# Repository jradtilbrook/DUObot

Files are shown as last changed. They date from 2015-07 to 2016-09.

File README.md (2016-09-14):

# DUObot Project Repository

This repository contains the files related to my two-wheeled balancing robot, aptly named DUObot.

In the extremely rare circumstance that someone actually uses this repository and/or finds a bug, please let me know by opening an issue. I would also welcome any other feedback or contributions.

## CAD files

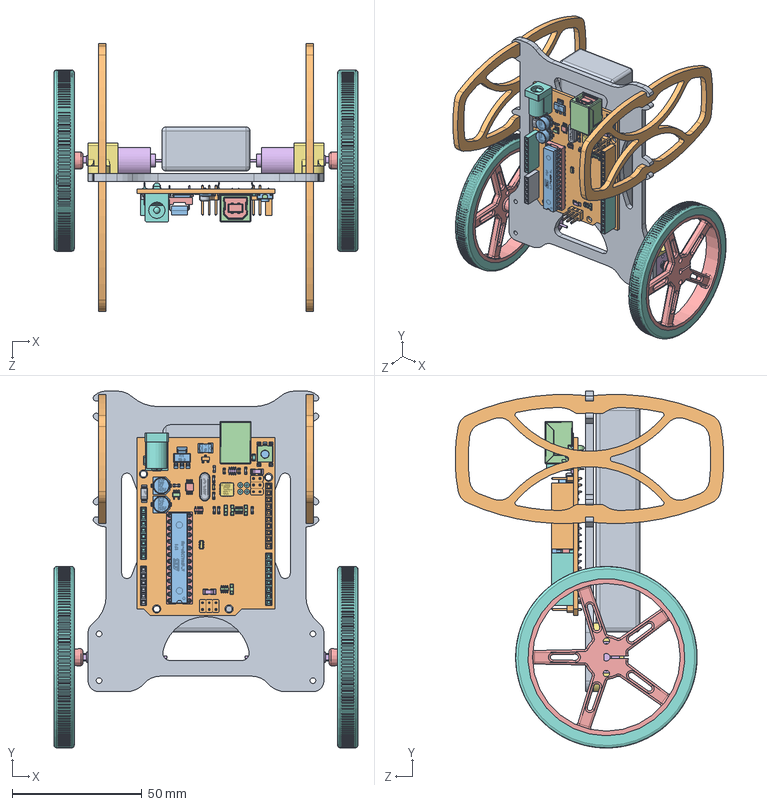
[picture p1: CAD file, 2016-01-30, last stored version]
cad/DUObot.SLDASM
117.2 x 137.7 x 103.6 mm
riser
unoboard blue
47uf CAP Dcase x 2
USB SHELL
USB core
usb top contact x 2
usb btm contact x 2
power jack
crystal
2pin_header__02 x 6
nano - reg
led x 4
dip28
dip socket pin x 28
atmega16u2
8 PORT HEADER x 2
6 PORT HEADER
10 PORT HEADER
ATMEL328P
102 RESISTOR PACK x 2
103 RESISTOR PACK
220 RESISTOR PACK
16mhz crystal - measured
PADS001
603 cap on pad x 8
ssot3
mf-msmf050-2
lmv358
lp2985dgkr
cd1206 diode x 2
603 resistor
blm21
m7 diode
MLC0603 x 2
RESET CORE
RESET
Pololu 70mm Wheel x 2
12mm Motor Gearbox x 2
mount x 2
Pololu 70mm Tire x 2
battery
guard x 2

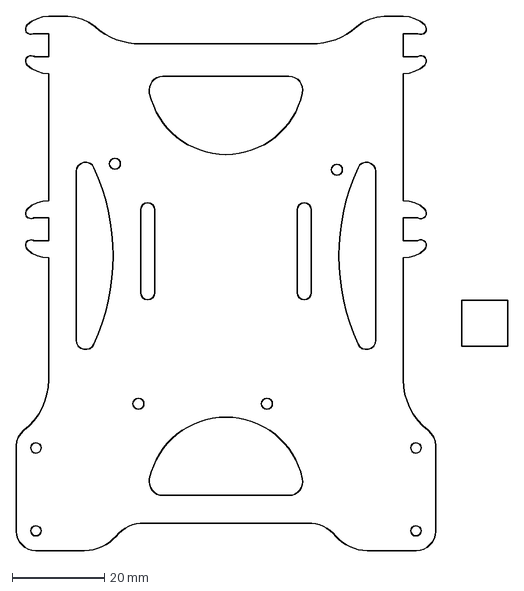
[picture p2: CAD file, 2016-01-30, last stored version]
cad/riser_final.dxf
106.7 x 116.0 mm

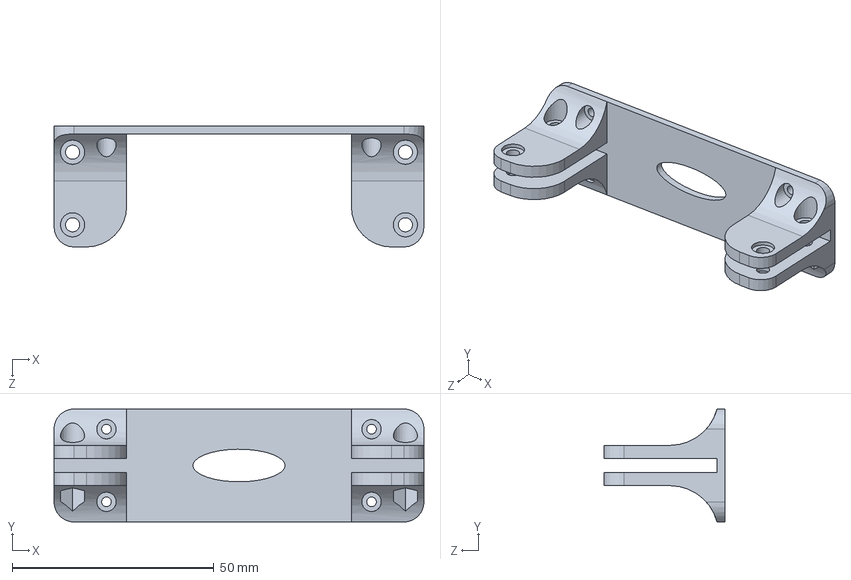
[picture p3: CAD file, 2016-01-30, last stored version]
cad/motor-riser-adapter.SLDPRT
91.7 x 28.0 x 30.0 mm

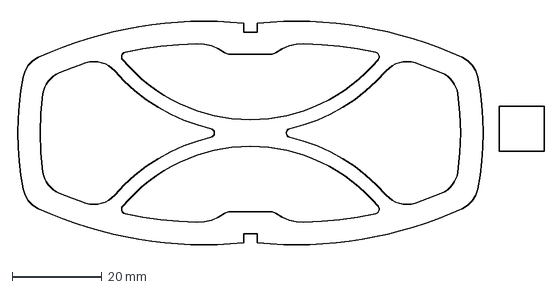
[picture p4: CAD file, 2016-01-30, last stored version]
cad/guard_final.dxf
117.6 x 52.0 mm

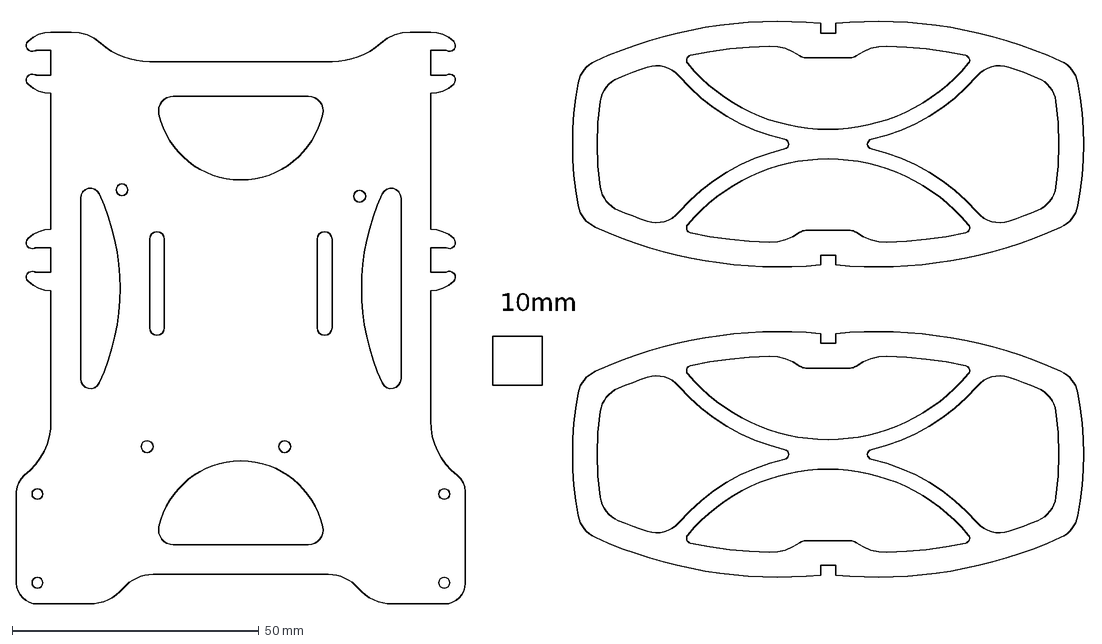
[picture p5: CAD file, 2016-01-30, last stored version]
cad/DUO_mk4.dxf
10mm

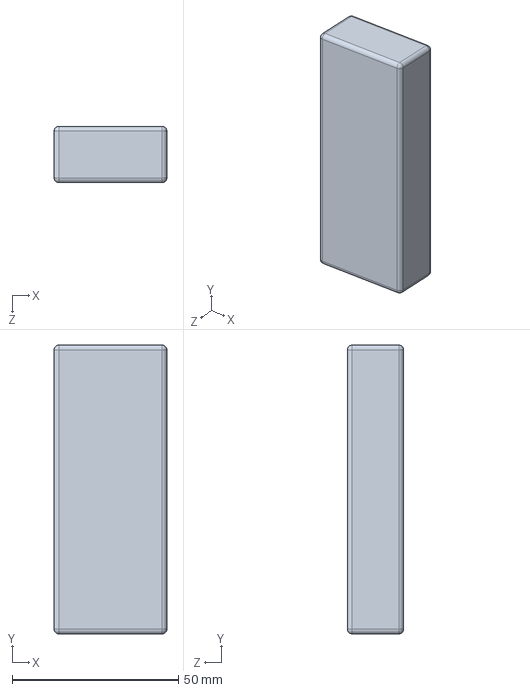
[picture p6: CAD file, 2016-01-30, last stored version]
cad/battery.SLDPRT
34.0 x 87.0 x 17.0 mm

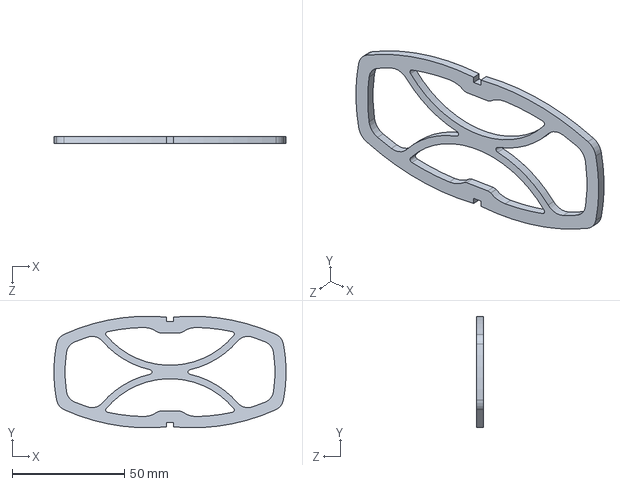
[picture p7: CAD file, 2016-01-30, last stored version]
cad/guard.SLDPRT
103.6 x 49.8 x 3.00 mm

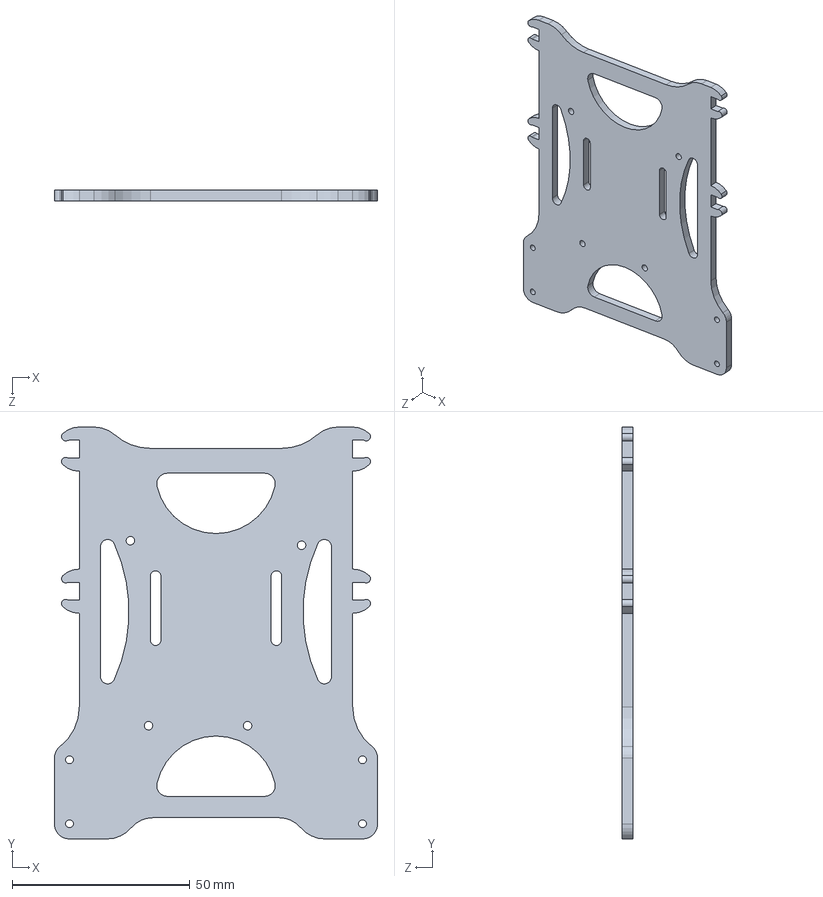
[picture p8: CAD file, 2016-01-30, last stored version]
cad/riser.SLDPRT
91.0 x 116.0 x 3.00 mm

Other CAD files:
cad/DUO_mk4.dwg
cad/guard.DXF
cad/motor-riser-adapter.STL
cad/riser.DXF

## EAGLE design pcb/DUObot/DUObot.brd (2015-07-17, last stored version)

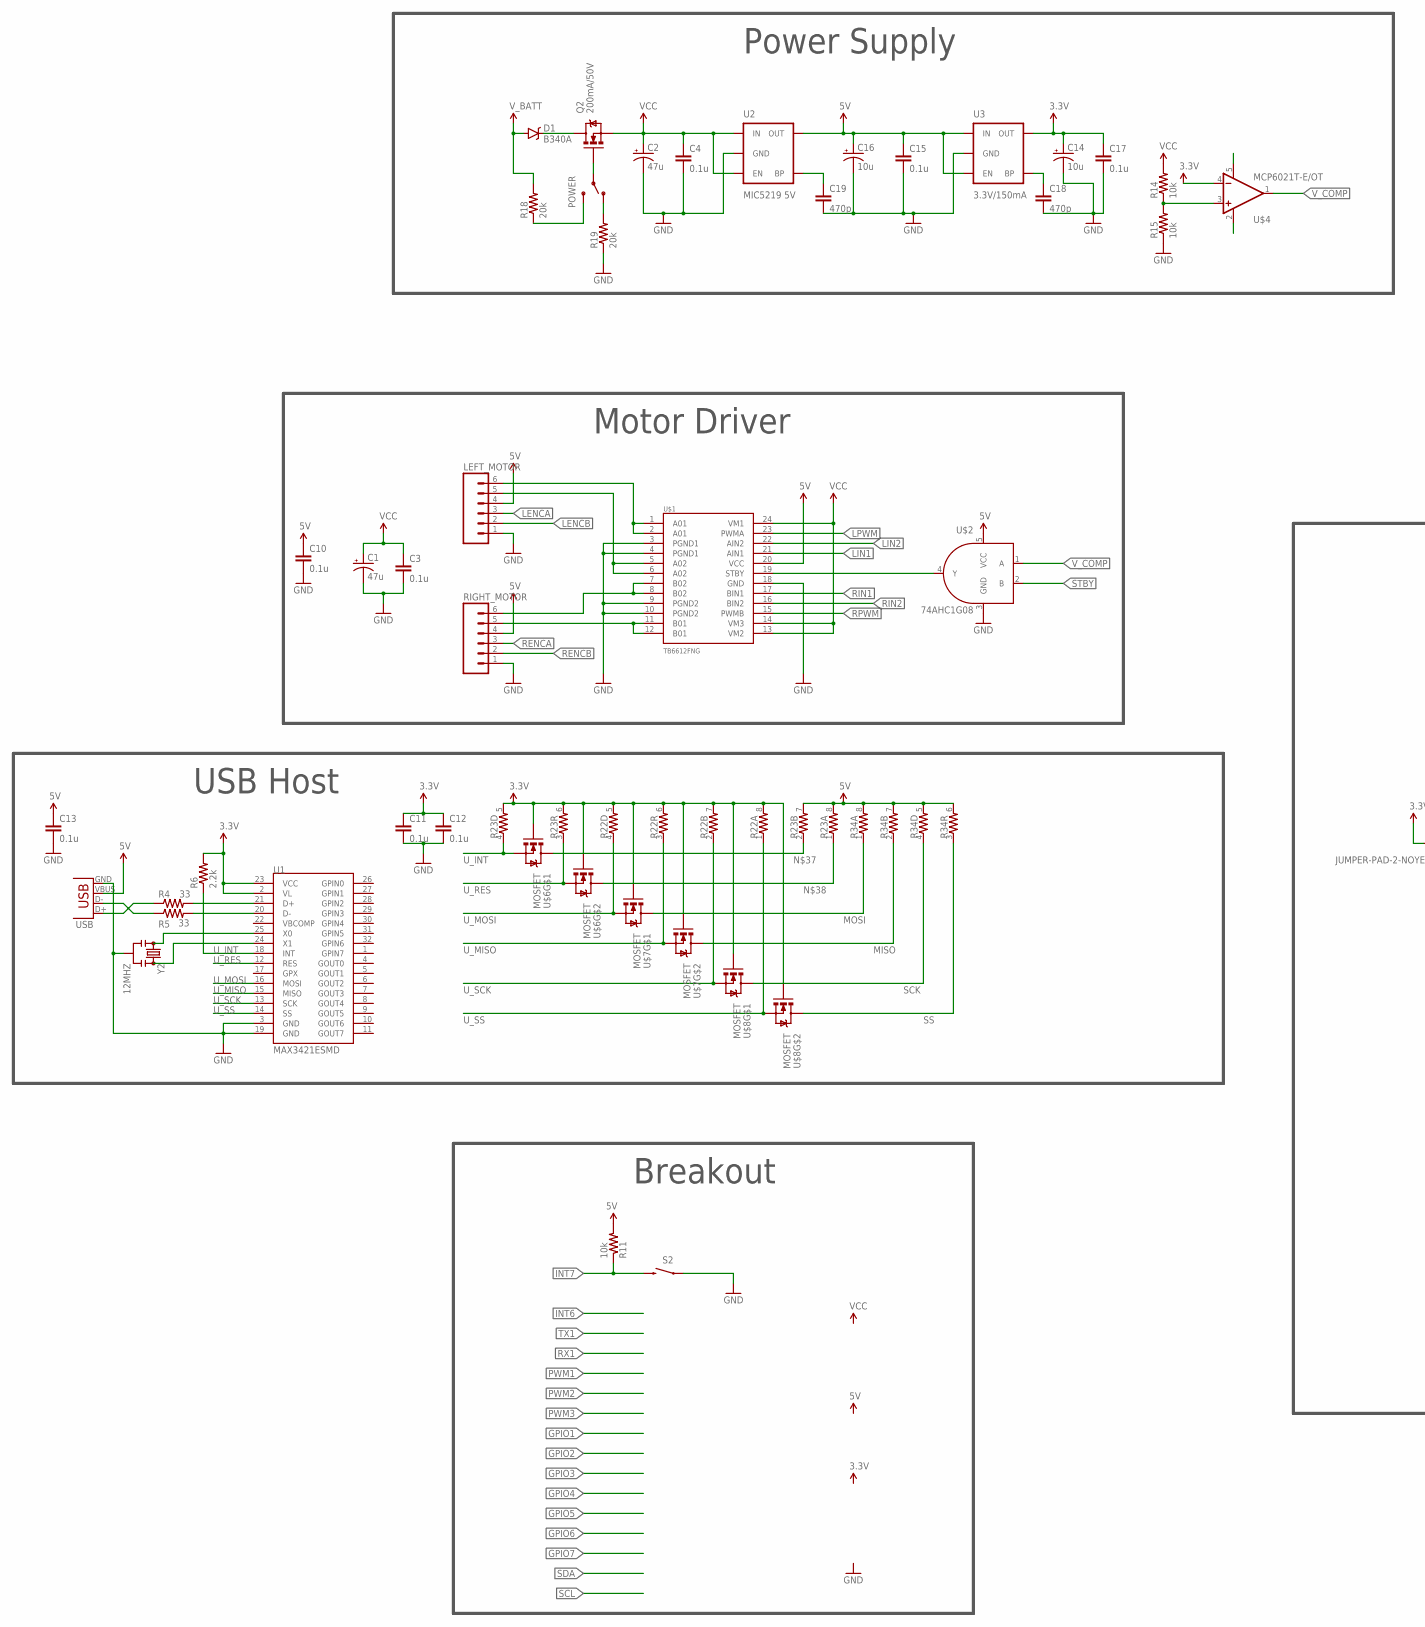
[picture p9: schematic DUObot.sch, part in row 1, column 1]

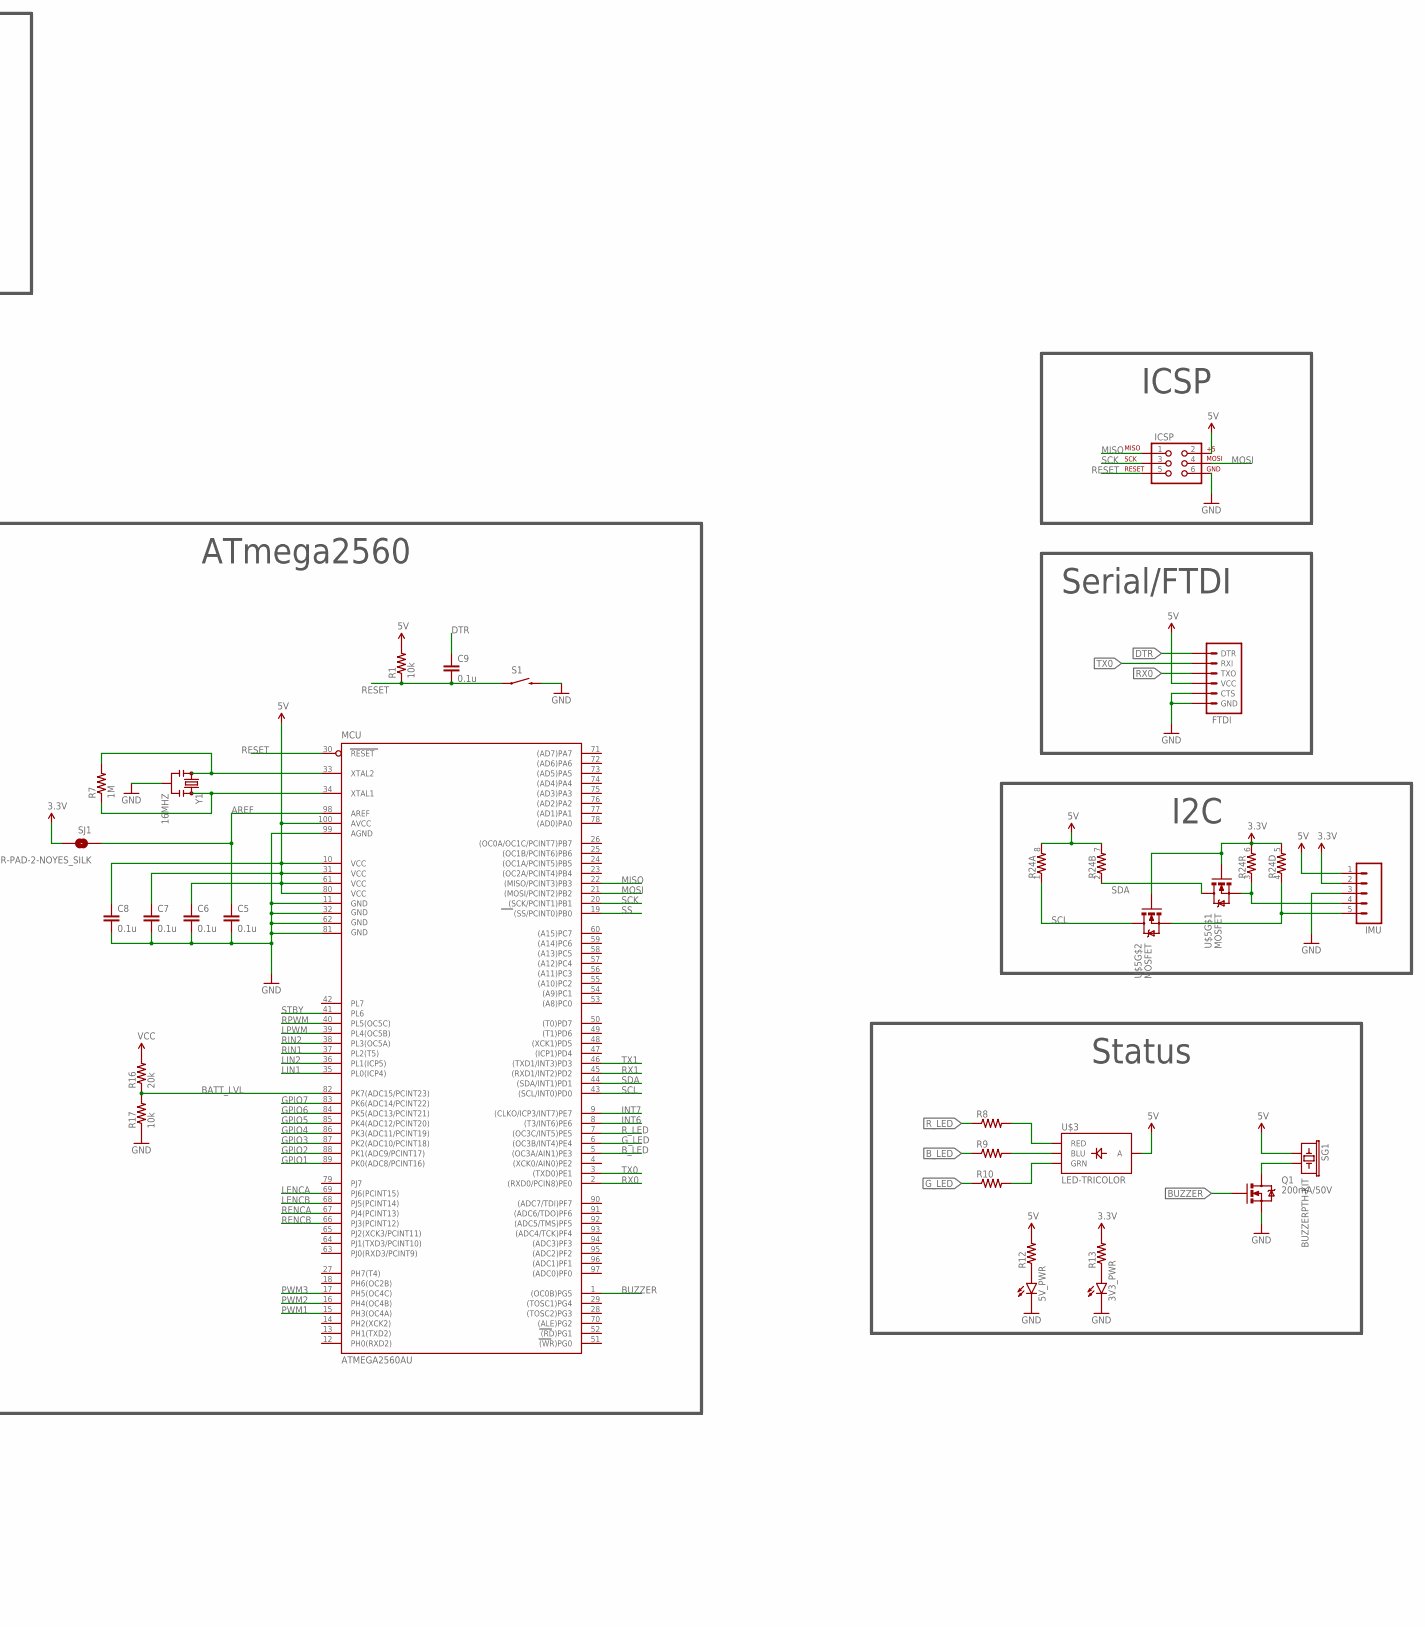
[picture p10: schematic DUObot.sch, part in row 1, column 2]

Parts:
3V3_PWR, 5V_PWR: LED0805; LED-0805
C1, C2: 47u; PANASONIC_D
C3, C4, C5, C6, C7, C8, C9, C10, C11, C12, C13, C15, C17: 0.1u; 0805
C14, C16: 10u; EIA3216
C18, C19: 470p; 0805
D1: B340A; SMA-DIODE
FTDI: ARDUINO_SERIAL_PROGRAMPTH; 1X06
ICSP: AVR_SPI_PRG_6TESTPOINTS; 2X3_TEST_POINTS
IMU: M05SMD2; 1X05-1MM-RA
LEFT_MOTOR: M06SMD-1MM; 1X06-1MM
MCU: ATMEGA2560AU; TQFP100
POWER: SWITCH-SPDT-SMD-A; SWITCH-SPST-SMD-A
Q1, Q2: 200mA/50V; SOT23-3
R1, R11, R14, R15, R17: 10k; 0805
R4, R5: 33; 0805
R6: 2.2k; 0805
R7: 1M; 0805
R8, R9, R10, R12, R13: RESISTOR0805-RES; 0805
R16, R18, R19: 20k; 0805
R22, R23, R24, R34: RESISTOR-ARRAY0603-ARV; 0603-ARV
RIGHT_MOTOR: M06SMD-1MM; 1X06-1MM
S1, S2: SWITCH-MOMENTARY-2SMD-4; TACTILE_SWITCH_TALL
SG1: BUZZERPTH-KIT; BUZZER-12MM-KIT
SJ1: JUMPER-PAD-2-NOYES_SILK; PAD-JUMPER-2-NO_YES_SILK
U1: MAX3421ESMD; TQFP32-5MM
U2: MIC5219 5V; SOT23-5
U3: 3.3V/150mA; SOT23-5
U$1: TB6612FNG; SSOP24
U$2: 74AHC1G08; SOT353
U$3: LED-TRICOLOR; LED-TRICOLOR-SMD
U$4: MCP6021T-E/OT; SOT23-5
U$5, U$6, U$7, U$8: MOSFET; SOT363_V2
USB: USB-A-SMD; USB-A-S-NOSILK-FEMALE
Y1: 16MHZ; RESONATOR-SMD
Y2: 12MHZ; RESONATOR-SMD

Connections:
3.3V: C11.1, C12.1, C14.A (+), C17.1, IMU.2, R6.2, R13.2, R22.5 (2), R22.6 (2), R22.7 (2), R22.8 (2), R23.5 (2), R23.6 (2), R24.5 (2), R24.6 (2), SJ1.2, U1.2 (VL), U1.23 (VCC), U3.5 (OUT), U$4.4 (-IN), U$5.G1 (G), U$5.G2 (G), U$6.G1 (G), U$6.G2 (G), U$7.G1 (G), U$7.G2 (G), U$8.G1 (G), U$8.G2 (G)
5V: C6.1, C7.1, C8.1, C10.1, C13.1, C15.1, C16.A (+), FTDI.4 (VCC), ICSP.2, IMU.1, LEFT_MOTOR.4, MCU.10 (VCC), MCU.31 (VCC1), MCU.61 (VCC2), MCU.80 (VCC3), MCU.100 (AVCC), R1.2, R11.2, R12.2, R23.7 (2), R23.8 (2), R24.7 (2), R24.8 (2), R34.5 (2), R34.6 (2), R34.7 (2), R34.8 (2), RIGHT_MOTOR.4, SG1.+ (1), U2.5 (OUT), U3.1 (IN), U3.3 (EN), U$1.20 (VCC), U$2.5 (VCC), U$3.A, USB.VBUS
AREF: C5.1, MCU.98 (AREF), SJ1.1
BATT_LVL: MCU.82 (PK7(ADC15/PCINT23)), R16.1, R17.2
BUZZER: MCU.1 ((OC0B)PG5), Q1.1 (G)
B_LED: MCU.5 ((OC3A/AIN1)PE3), R9.1
DTR: C9.1, FTDI.1 (DTR)
GND: 3V3_PWR.CATHODE (C), 5V_PWR.CATHODE (C), C1.-, C2.-, C3.2, C4.2, C5.2, C6.2, C7.2, C8.2, C10.2, C11.2, C12.2, C13.2, C14.C (-), C15.2, C16.C (-), C17.2, C18.2, C19.2, FTDI.5 (CTS), FTDI.6 (GND), ICSP.6, IMU.3, LEFT_MOTOR.1, MCU.11 (GND), MCU.32 (GND1), MCU.62 (GND2), MCU.81 (GND3), MCU.99 (AGND), Q1.2 (S), R15.1, R17.1, R19.1, RIGHT_MOTOR.1, S1.B2 (2), S2.A2 (1), U1.3 (GND), U1.19 (GND), U2.2 (GND), U3.2 (GND), U$1.3 (PGND1), U$1.4 (PGND1), U$1.9 (PGND2), U$1.10 (PGND2), U$1.18 (GND), U$2.3 (GND), USB.GND, Y1.2, Y2.2
GPIO1: MCU.89 (PK0(ADC8/PCINT16))
GPIO2: MCU.88 (PK1(ADC9/PCINT17))
GPIO3: MCU.87 (PK2(ADC10/PCINT18))
GPIO4: MCU.86 (PK3(ADC11/PCINT19))
GPIO5: MCU.85 (PK4(ADC12/PCINT20))
GPIO6: MCU.84 (PK5(ADC13/PCINT21))
GPIO7: MCU.83 (PK6(ADC14/PCINT22))
G_LED: MCU.6 ((OC3B/INT4)PE4), R10.1
INT6: MCU.8 ((T3/INT6)PE6)
INT7: MCU.9 ((CLKO/ICP3/INT7)PE7), R11.1, S2.B2 (2)
LENCA: LEFT_MOTOR.3, MCU.69 (PJ6(PCINT15))
LENCB: LEFT_MOTOR.2, MCU.68 (PJ5(PCINT14))
LIN1: MCU.35 (PL0(ICP4)), U$1.21 (AIN1)
LIN2: MCU.36 (PL1(ICP5)), U$1.22 (AIN2)
LPWM: MCU.39 (PL4(OC5B)), U$1.23 (PWMA)
MISO: ICSP.1, MCU.22 ((MISO/PCINT3)PB3), R34.2 (1), U$7.D2 (D)
MOSI: ICSP.4, MCU.21 ((MOSI/PCINT2)PB2), R34.1, U$7.D1 (D)
unnamed: RIGHT_MOTOR.5, U$1.11 (B01), U$1.12 (B01)
unnamed: RIGHT_MOTOR.6, U$1.7 (B02), U$1.8 (B02)
unnamed: LEFT_MOTOR.6, U$1.1 (A01), U$1.2 (A01)
unnamed: LEFT_MOTOR.5, U$1.5 (A02), U$1.6 (A02)
unnamed: MCU.33 (XTAL2), R7.2, Y1.1
unnamed: MCU.34 (XTAL1), R7.1, Y1.3
unnamed: R4.1, USB.D+
unnamed: R5.2, U1.20 (D-)
unnamed: R4.2, U1.21 (D+)
unnamed: R5.1, USB.D-
unnamed: R14.1, R15.2, U$4.3 (+IN)
unnamed: U$1.19 (STBY), U$2.4 (Y)
unnamed: Q1.3 (D), SG1.- (2)
unnamed: R9.2, U$3.B (BLU)
unnamed: R8.2, U$3.R (RED)
unnamed: R10.2, U$3.G (GRN)
unnamed: 5V_PWR.ANODE (A), R12.1
unnamed: 3V3_PWR.ANODE (A), R13.1
unnamed: U1.25 (X0), Y2.1
unnamed: U1.24 (X1), Y2.3
unnamed: C19.1, U2.4 (BP)
unnamed: C18.1, U3.4 (BP)
unnamed: D1.C, Q2.3 (D)
unnamed: POWER.1 (O), R19.2
unnamed: POWER.3 (S), R18.1
unnamed: POWER.2, Q2.1 (G)
unnamed: IMU.4, R24.3 (1), U$5.S1 (S)
unnamed: IMU.5, R24.4 (1), U$5.S2 (S)
unnamed: R23.2 (1), U$6.D1 (D)
unnamed: R23.1, U$6.D2 (D)
PWM1: MCU.15 (PH3(OC4A))
PWM2: MCU.16 (PH4(OC4B))
PWM3: MCU.17 (PH5(OC4C))
RENCA: MCU.67 (PJ4(PCINT13)), RIGHT_MOTOR.3
RENCB: MCU.66 (PJ3(PCINT12)), RIGHT_MOTOR.2
RESET: C9.2, ICSP.5, MCU.30 (RESET), R1.1, S1.A2 (1)
RIN1: MCU.37 (PL2(T5)), U$1.17 (BIN1)
RIN2: MCU.38 (PL3(OC5A)), U$1.16 (BIN2)
RPWM: MCU.40 (PL5(OC5C)), U$1.15 (PWMB)
RX0: FTDI.3 (TXO), MCU.2 ((RXD0/PCIN8)PE0)
RX1: MCU.45 ((RXD1/INT2)PD2)
R_LED: MCU.7 ((OC3C/INT5)PE5), R8.1
SCK: ICSP.3, MCU.20 ((SCK/PCINT1)PB1), R34.4 (1), U$8.D1 (D)
SCL: MCU.43 ((SCL/INT0)PD0), R24.1, U$5.D2 (D)
SDA: MCU.44 ((SDA/INT1)PD1), R24.2 (1), U$5.D1 (D)
SS: MCU.19 ((SS/PCINT0)PB0), R34.3 (1), U$8.D2 (D)
STBY: MCU.41 (PL6), U$2.2 (B)
TX0: FTDI.2 (RXI), MCU.3 ((TXD0)PE1)
TX1: MCU.46 ((TXD1/INT3)PD3)
U_INT: R6.1, R23.4 (1), U1.18 (INT), U$6.S1 (S)
U_MISO: R22.3 (1), U1.15 (MISO), U$7.S2 (S)
U_MOSI: R22.4 (1), U1.16 (MOSI), U$7.S1 (S)
U_RES: R23.3 (1), U1.12 (RES), U$6.S2 (S)
U_SCK: R22.2 (1), U1.13 (SCK), U$8.S1 (S)
U_SS: R22.1, U1.14 (SS), U$8.S2 (S)
VCC: C1.+, C2.+, C3.1, C4.1, Q2.2 (S), R14.2, R16.2, U2.1 (IN), U2.3 (EN), U$1.13 (VM2), U$1.14 (VM3), U$1.24 (VM1)
V_BATT: D1.A, R18.2
V_COMP: U$2.1 (A), U$4.1 (OUT)

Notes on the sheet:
ICSP
Serial/FTDI
I2C
Motor Driver
USB Host
ATmega2560
Power Supply
Status
Breakout

Board: 2 copper layers, 70 parts (1 on the bottom side), 70 nets, no tracks yet.

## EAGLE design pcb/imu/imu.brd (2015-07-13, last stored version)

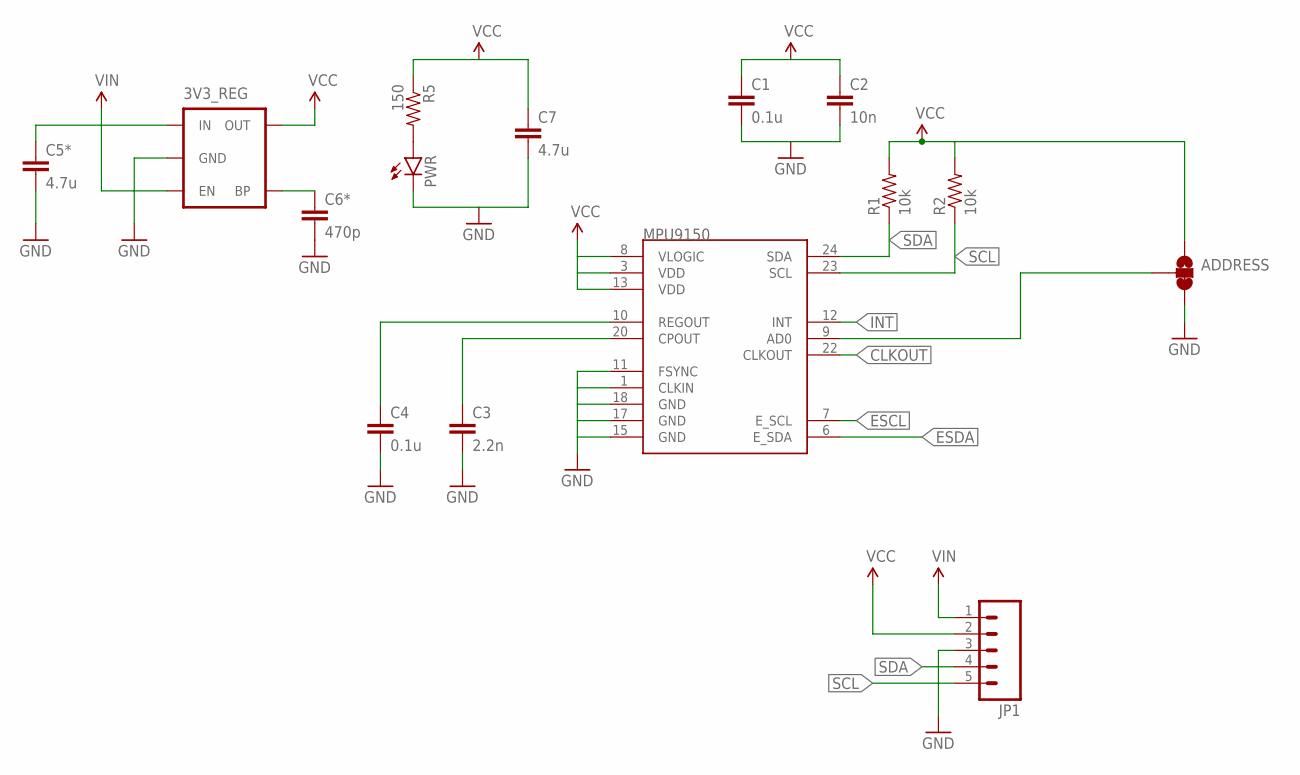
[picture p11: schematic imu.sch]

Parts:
3V3_REG: MIC52053.3V; SOT23-5
ADDRESS: JUMPER-PAD-3-2OF3_NC_BY_TRACE_SMALL; PAD-JUMPER-3-2OF3_NC_BY_TRACE_YES_SILK_FULL_BOX
C1, C4: 0.1u; 0805
C2: 10n; 0805
C3: 2.2n; 0805
C5*, C7: 4.7u; 0805
C6*: 470p; 0805
JP1: M05SMD2; 1X05-1MM-RA
MPU9150: MPU-9150QFN-24-NP; QFN-24-NP
PWR: LED0805; LED-0805
R1, R2: 10k; 0805
R5: 150; 0805

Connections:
AD0: ADDRESS.2, MPU9150.9 (AD0)
CLKOUT: MPU9150.22 (CLKOUT)
ESCL: MPU9150.7 (E_SCL)
ESDA: MPU9150.6 (E_SDA)
GND: 3V3_REG.2 (GND), ADDRESS.3, C1.2, C2.2, C3.2, C4.2, C5*.2, C6*.2, C7.2, JP1.3, MPU9150.1 (CLKIN), MPU9150.11 (FSYNC), MPU9150.15 (GND), MPU9150.17 (GND), MPU9150.18 (GND), PWR.CATHODE (C)
INT: MPU9150.12 (INT)
unnamed: PWR.ANODE (A), R5.2
unnamed: C3.1, MPU9150.20 (CPOUT)
unnamed: C4.1, MPU9150.10 (REGOUT)
unnamed: 3V3_REG.4 (BP), C6*.1
SCL: JP1.5, MPU9150.23 (SCL), R2.1
SDA: JP1.4, MPU9150.24 (SDA), R1.1
VCC: 3V3_REG.5 (OUT), ADDRESS.1, C1.1, C2.1, C7.1, JP1.2, MPU9150.3 (VDD), MPU9150.8 (VLOGIC), MPU9150.13 (VDD), R1.2, R2.2, R5.1
VIN: 3V3_REG.1 (IN), 3V3_REG.3 (EN), C5*.1, JP1.1

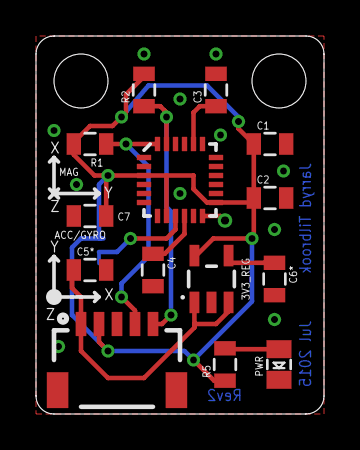
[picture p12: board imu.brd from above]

Board: 2 copper layers, 16.0 x 21.0 mm, 15 parts (1 on the bottom side), 10 nets.

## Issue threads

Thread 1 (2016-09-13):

Battery case prototype

jradtilbrook, 2016-09-13:
Draw and print a prototype battery pack for DUObot.
Should be able to house 4 or 5, AA or AAA batteries so that alkaline or NiMH can be used, but the output is always 6V nominal. The different sizes are required depending on the performance and weight handling of the motors.

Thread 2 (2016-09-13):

IMU interface library

jradtilbrook, 2016-09-13:
IMU is most likely going to be MPU9250 from InvenSense. A I2C or SPI interface library is needed to communicate with it. Either use some existing libraries, create a new one, or a mix of the two.

Plan is just to be able to talk to it in an asynchronous way, allowing the use of an interrupt based algorithm as opposed to an iterative, polling algorithm.

IMU filtering will be a separate task.

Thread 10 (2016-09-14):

Design and print frame

jradtilbrook, 2016-09-14:
After #1, design the chassis for DUObot. Needs to mount motors, pyboard/shield and battery pack. Making it relatively small is preferable (similar to BeagleMiP).

jradtilbrook, 2016-09-14:
Possible other things:
- arms/barriers for falling over
- carrying objects
- ???

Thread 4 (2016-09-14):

Motor control module

jradtilbrook, 2016-09-14:
Finish the motor control module. Current setup looks good, just needs finishing off.

End result: Be able to control the speed and direction of each motor.

Possible extension: Use the encoder as feedback from within the motor control module to give a better speed/position feedback loop.

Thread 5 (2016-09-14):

Design and order PCB

jradtilbrook, 2016-09-14:
Figure out all components required/wanted. Finalise a prototype circuit to test all components.

Design the custom shield for the pyboard and order it from OSH park. Also consider the extension to Arduino in future versions. This could either use the same shield, or be a new all-inclusive single board version.

Turn around from ordering is around 21 days, so this needs to be done early in the milestone.

jradtilbrook, 2016-09-14:
- [ ] Need to select the components (active and passive)
- [ ] Also need to figure out/prototype the power selection so motors cannot be powered whilst powered over usb
- [ ] Design the power switch to go through a mosfet so a small power switch can be used

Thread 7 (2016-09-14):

PS4 controller module

jradtilbrook, 2016-09-14:
Figure out how to connect and communicate with a PS4 controller. This may need doing before #5 is submitted to OSH park so that it can be included in the first version (although not necessary).

RN42 doesn't look like it will work (cannot get it to pair). Try nrf8001 from adafruit. This will require SPI library and decoding the messages received (if it pairs). If it works, PCB prototyping will most likely be required because a custom trace antenna will be required (as in the adafruit breakout).

jradtilbrook, 2016-09-14:
Would also be good to allow an app (apple or android) to control, or even a custom bluetooth controller (eg using an arduino)

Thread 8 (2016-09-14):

PID/controller module

jradtilbrook, 2016-09-14:
Code the fusion between the IMU and motor controller to give the ability to balance. This will need thorough testing and tweaking to get right.

Be sure to test it in a loud environment (music), that's what seemed (?) to break it last time.

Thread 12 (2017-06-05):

Encoder class incorrectly handles overflow

jradtilbrook, 2017-06-05:
The over/under flow from TIMER_MAX to 0 is actually one tick, but the output of the ticks() shows no change between both of these values. Probably not a big deal since its one tick per overflow, unless somehow we are constantly going back and forth at the overflow point will cause major drift!

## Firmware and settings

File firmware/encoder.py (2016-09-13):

from pyb import Pin, Timer, LED

class Encoder():
    """
    Abstracts a quadrature encoder to give a tick count.
    The count is a signed integer starting at zero. It wraps the count from the
    attached timer to give a seamless and continuous tick count. Overflows of
    the internal timer counter register should be adequatly handled. If
    overflows or weird behaviour occurs around the overflow points, try
    increasing Encoder.HYSTERESIS.
    Note: Only works on pin pairs 'X1' & 'X2', 'X9' & 'X10', or 'Y1', 'Y2'. The
    timer will be automatically selected. Both Timer 2 and 5 work for 'X1' &
    'X2', but Timer 5 is preferred because Timer 2 is used for LED PWM but both
    can be used by changing the values of Encoder.AF_MAP.
    """
    # Constant for decoding in single line mode
    SINGLE_MODE = Timer.ENC_A
    # Constant for decoding in quad mode
    DUAL_MODE = Timer.ENC_AB
    # Maps alternate pin function descriptions to the required timer number
    TIMER_MAP = {'AF1_TIM2': 2, 'AF2_TIM4': 4, 'AF2_TIM5': 5, 'AF3_TIM8': 8}
    # Maps pin names to the alternate function to use
    AF_MAP = {'X1' : 'AF2_TIM5', 'X2': 'AF2_TIM5', 'X9': 'AF2_TIM4',
              'X10': 'AF2_TIM4', 'Y1': 'AF3_TIM8', 'Y2': 'AF3_TIM8'}
    # Defines the pin pairs that must be used
    PIN_PAIRS = [['X1','X9','Y1'],['X2','X10','Y2']]
    # Hysteresis value to overflow detection
    HYSTERESIS = 12 # One full rotation of encoder

    def __init__(self, pinA, pinB, mode = DUAL_MODE):
        """
        Instantiate an Encoder object.
        Initalises the Pins, Timer and TimerChannel for use as a quadrature
        decoder. Registers an overflow callback to elegantly handle counter
        register overflows.
        pinA: Any valid value taken by pyb.Pin constructor
        pinB: Any valid value taken by pyb.Pin constructor
        mode: Mode to use for decoding (Encoder.SINGLE_MODE or
                Encoder.DUAL_MODE)
        raises: Any exception thrown by pyb.Pin, pyb.Timer, pyb.Timer.channel
                or Exception if pins are not compatible pairs
        """
        self._chA = Pin(pinA)
        self._chB = Pin(pinB)
        self._ticks = 0

        # Check pins are compatible
        self._checkPins(pinA, pinB)

        # init pins for alternate encoder function
        af = self.AF_MAP[self._chA.names()[1]]
        channel = self.TIMER_MAP[af]
        af = getattr(Pin, af)
        self._chA.init(Pin.AF_PP, pull = Pin.PULL_NONE, af = af)
        self._chB.init(Pin.AF_PP, pull = Pin.PULL_NONE, af = af)
        # init timer
        self._timer = Timer(channel, prescaler = 0, period = 100000)
        # init encoder mode
        # self._channel = self._timer.channel(1, mode)
        self._timer.channel(1, mode)
        # setup overflow callback
        self._timer.callback(self._overflow)
        # init count register to middle of count
        self._timer.counter(self._timer.period()//2)
        self._lastRead = self._timer.counter()

    def _checkPins(self, pinA, pinB):
        """
        Check that two pins can be used for a decoding and are on the same
        timer.
        """
        try:
            if pinA in self.PIN_PAIRS[0]:
                if self.PIN_PAIRS[0].index(pinA) != self.PIN_PAIRS[1].index(pinB):
                    raise Exception()
            elif pinA in self.PIN_PAIRS[1]:
                if self.PIN_PAIRS[0].index(pinB) != self.PIN_PAIRS[1].index(pinA):
                    raise Exception()
            else:
                raise Exception()
        except:
            raise Exception(pinA + ' & ' + pinB + ' are not on the same Timer')

    def ticks(self, ticks = None):
        """
        Get or set the current tick count.
        Ticks is a signed integer.
        """
        if ticks is not None: # set ticks to desired value
            self._ticks = ticks
        else: # retrieve latest count and update internals
            count = self._timer.counter()
            self._ticks = self._ticks + (count - self._lastRead)
            self._lastRead = count
        return self._ticks

    def _overflow(self, timer):
        """
        Timer overflow callback to gracefully handle overflow events. If
        weird things are occurring, try increasing the HYSTERESIS value.
        """
        count = timer.counter()
        if 0 <= count <= self.HYSTERESIS: # overflow
            self._ticks = self._ticks + (timer.period() - self._lastRead + count)
            self._lastRead = count
        elif (timer.period() - self.HYSTERESIS) <= count <= timer.period(): # underflow
            self._ticks = self._ticks - (self._lastRead + timer.period() - count)
            self._lastRead = count
        else: # hysteresis not big enough
            #LED(1).on() # turn on inbuilt red led to show error
            pass

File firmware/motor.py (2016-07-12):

from pyb import Pin

class Motor:
    def __init__(self, pinA, pinB):
        self._a = Pin(pinA, Pin.OUT_PP) #todo: check motor driver pins for internal pull resistors. or use pyboard pin pulling and open drain?
        self._b = Pin(pinB, Pin.OUT_PP)
        self.stop()

    # defaults to connect both terminals to GND, but can override to VCC
    def stop(self, val = False):
        self._a.value(val)
        self._b.value(val)

    def drive(self, direction):
        if direction > 0:
            self._a.high()
            self._b.low()
        elif direction == 0:
            self.stop()
        elif direction < 0:
            self._a.low()
            self._b.high()

class MotorPWM(Motor):
    def __init__(self, a, b, p):
        super(MotorPWM, self).__init__(a, b)
        self._p = Pin(p, Pin.AF_PP, af = ???)

    def stop(self):
        pass

    def freewheel(self):
        pass

    def drive(self, speed):
        pass

class MotorDriver:
    def __init__(self, a, b, p, c, d, q, e):
        self._left = MotorPWM(a, b, p)
        self._right = MotorPWM(c, d, q)
        self._standby = Pin(e, Pin.OUT_PP)
        self._standby.high()

    # Automatically enables driver when setting speed
    def drive(self, left, right, enable = True):
        pass

    def driveL(self, speed, enable = True):
        pass

    def driveR(self, speed, enable = True):
        pass

    def stop(self):
        pass

    def stopL(self):
        pass

    def stopR(self):
        pass

    def freewheel(self):
        pass

    def freewheelL(self):
        pass

    def freewheelR(self):
        pass

    def enable(self):
        self._standby.low()

    def disable(self):
        self._standby.high()

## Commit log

2015-07-08 Add pcb design projects. Update README
    [DUObot.sch, imu.sch]
2015-07-08 Add blank Arduino sketch
2015-07-09 Add components to MPU breakout. Needs board layout and revision
    [imu.brd, imu.sch]
2015-07-09 Change LED to 0805 package
    [imu.brd, imu.sch]
2015-07-10 Finish MPU board layout revision 1
    [imu.brd, imu.sch]
2015-07-10 MPU revision 2 with 3mm holes
    [imu.brd, imu.sch]
2015-07-10 Add IMU axes to silkscreen
    [imu.brd]
2015-07-10 Finalise IMU board schematic/layout. Try to make 3D model (*.emn/emp) files
    [imu.brd, imu.sch]
2015-07-10 Update readme to reflect todo list
    [DUObot.sch]
2015-07-13 Revise IMU board - add date and board title
    [imu.brd]
2015-07-13 Finalise rev2 board, add IMU parts list
    [imu.brd, partslist_imu.ods]
2015-07-14 Add more components to main board. Start pcb layout
    [DUObot.brd, DUObot.sch]
2015-07-16 Continue adding components to schematic
    [DUObot.brd, DUObot.sch]
2015-07-16 Working on power select control circuitry
    [DUObot.brd, DUObot.sch]
2015-07-17 Finalise parts list for IMU breakout
    [partslist_imu.ods]
2015-07-17 Main board mostly finished - needs minor changes/additions
    [DUObot.brd, DUObot.sch]
2015-07-17 Change individual pull-up resistors to arrays
    [DUObot.brd, DUObot.sch]
2015-07-27 TODO: Upgrade imu to MPU-9250 for future revisions
2016-01-30 Add CAD models and MPU6050 datasheets
    [DUO_mk4.dwg, DUO_mk4.dxf, DUObot.SLDASM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]
2016-07-11 Remove old files ready for mkV
    [DUO_mk4.dwg, DUO_mk4.dxf, DUObot.SLDASM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]
2016-07-11 Add skeleton for motor module
2016-07-12 Implement Motor class methods

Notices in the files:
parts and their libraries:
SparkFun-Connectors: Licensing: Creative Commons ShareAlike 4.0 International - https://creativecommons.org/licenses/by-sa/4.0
